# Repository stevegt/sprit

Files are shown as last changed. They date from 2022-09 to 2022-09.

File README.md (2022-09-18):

# sprit

I/O interface between a Raspberry Pi and a Dynamixel XL-320 servo.
Other Dynamixel models may work too, as well as other serial bus
servos such as those from Hiwonder -- haven't tested.

The Sprit is similar to the Poppy Project's Pixl board:

- https://www.poppy-project.org/en/
- https://github.com/poppy-project/pixl/blob/master/circuit_maker/Pixl.PDF

The main differences between the Sprit and Pixl are in the power
subsystem -- the Sprit is optimized for stationary use, while the Pixl
is optimized for mobile use on batteries:

| load | Sprit | Pixl |
|---|---|---|
| Pi | USB | 7V barrel jack or batteries |
| 7V servos | | 7V barrel jack or batteries |
| 8V servos | 10.5-18V barrel jack | |

- Sprit accepts anything from 10.5 to 18V via the barrel jack and
  regulates that down to 8V power for the servos.  Sprit does not
  provide power for the Pi, so the Pi must be powered via USB.
- Pixl accepts 7V from barrel jack or batteries, passes that
  unregulated to the servos, and regulates it down to 5V to power the
  Pi, so the Pi does not need to be plugged into USB power.

## Oshpark prototype v0.2 bare board



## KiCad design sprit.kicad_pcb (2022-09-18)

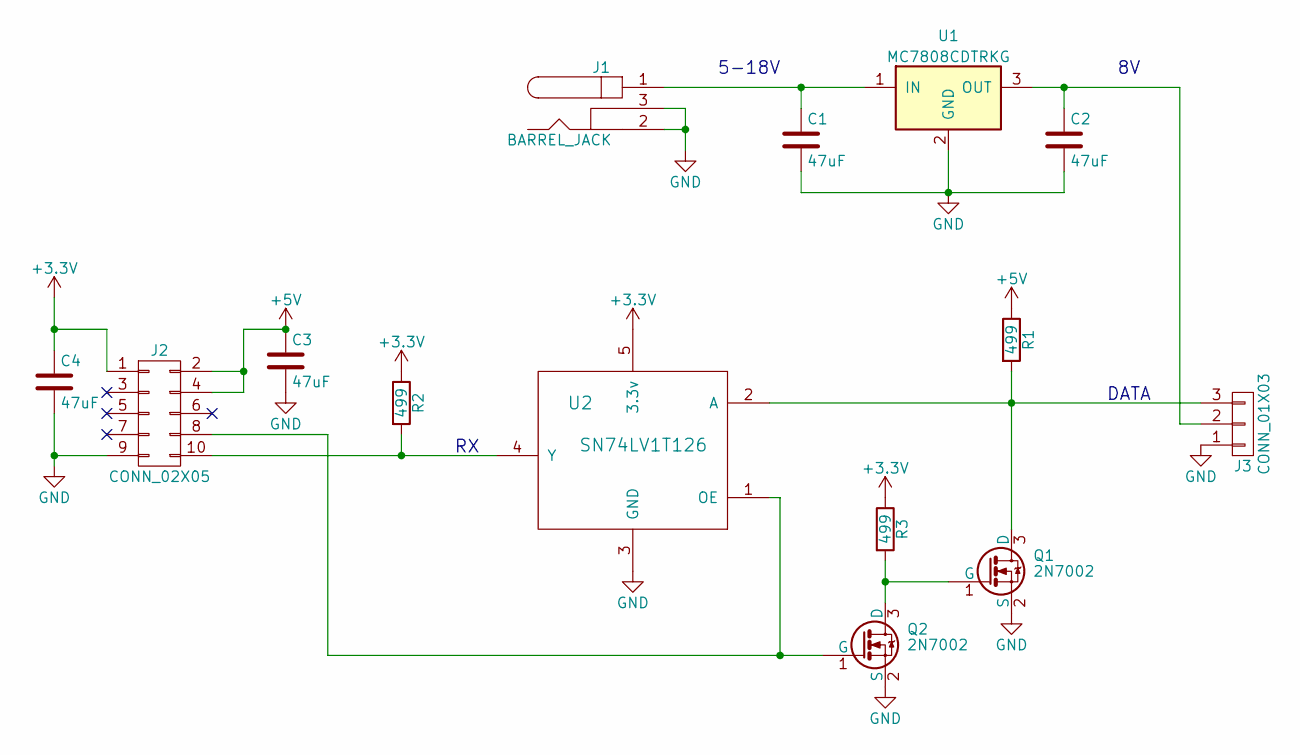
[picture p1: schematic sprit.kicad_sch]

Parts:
C1, C2, C3, C4: 47uF; C_1206_3216Metric
J1: BARREL_JACK; BarrelJack_Horizontal
J2: CONN_02X05; PinHeader_2x05_P2.54mm_Vertical
J3: CONN_01X03; Molex_Micro-Latch_53254-0370_1x03_P2.00mm_Horizontal
Q1, Q2: 2N7002; SOT-23
R1, R2, R3: 499; R_0805_2012Metric
U1: MC7808CDTRKG; TO-252-2
U2: SN74LV1T126; SOT-23-5

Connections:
+3V3: C4.1, J2.1, R2.1, R3.1, U2.5 (3.3v)
+5V: C3.1, J2.2, J2.4, R1.1
GND: C1.2, C2.2, C3.2, C4.2, J1.2, J1.3, J2.9, J3.1, Q1.2 (S), Q2.2 (S), U1.2 (GND), U2.3 (GND)
unnamed: C1.1, J1.1, U1.1 (IN)
unnamed: C2.1, J3.2, U1.3 (OUT)
unnamed: J2.8, Q2.1 (G), U2.1 (OE)
unnamed: J2.10, R2.2, U2.4 (Y)
unnamed: J3.3, Q1.3 (D), R1.2, U2.2 (A)
unnamed: Q1.1 (G), Q2.3 (D), R3.2

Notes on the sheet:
DATA
5-18V

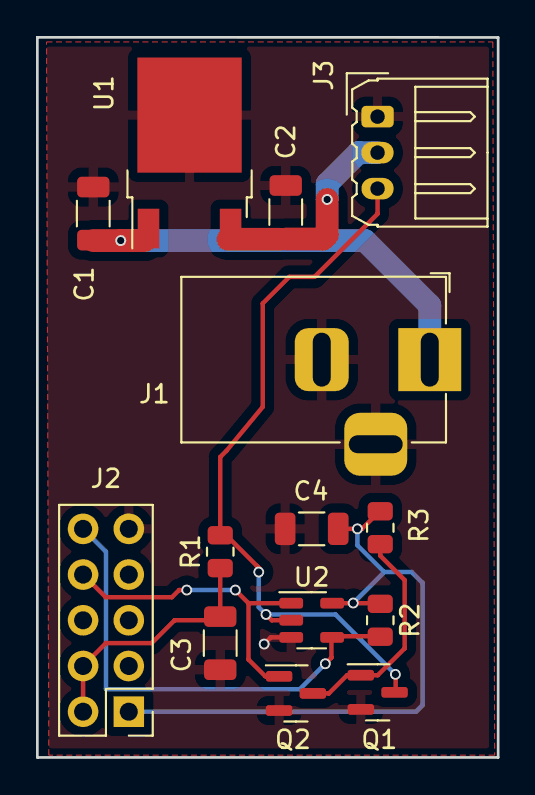
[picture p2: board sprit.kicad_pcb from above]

Board: 2 copper layers, 25.6 x 40.0 mm, 14 parts (0 on the bottom side), 9 nets.

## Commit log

2018-08-13 import of first alpha version as built
    [sprit-B.Cu.gbl, sprit-B.Mask.gbs, sprit-B.Paste.gbp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]
2022-09-17 WIP rework layout
    - checkpoint of 2018 changes found in repo
    - used kicad 4.0.7 as of 2018
    - apparent work in progress:
    - enlarge board
    - recess barrel jack
    - move J3 connector to opposite edge
    - configure autorouter
    [sprit.dsn]
2022-09-17 finish layout rework started 4 years ago(!)
    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
    [sprit.kicad_pcb]
2022-09-18 upgrade to kicad 6.0.7
    - v0.2 as ordered from oshpark
    - replace footprints
    - add pdf of 2017 mouser order
    [sprit.kicad_pcb, sprit.kicad_sch]
2022-09-18 fix supply voltage notation, add README
    [sprit.kicad_sch]
